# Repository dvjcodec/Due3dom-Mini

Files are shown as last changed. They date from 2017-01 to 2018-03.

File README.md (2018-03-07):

# DUE3DOM MINI

Modular 3D printer driver working as a shield for 32-bit ARM based Arduino DUE.

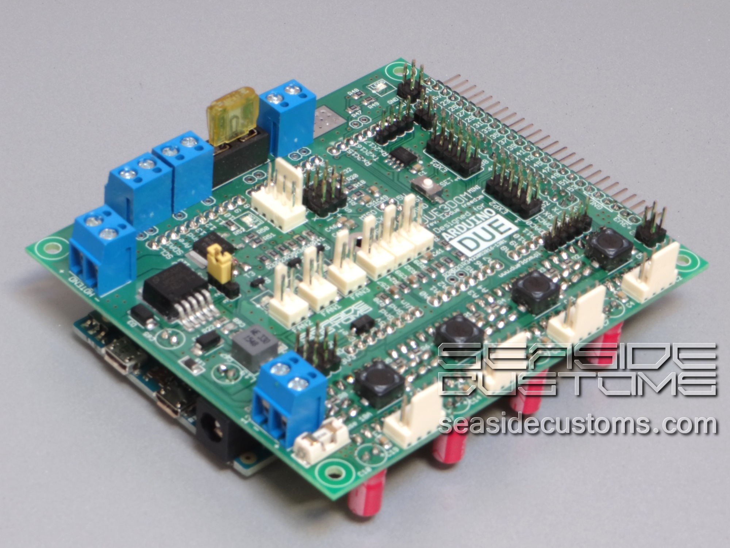
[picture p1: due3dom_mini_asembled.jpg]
Board


## Features:
* 20A channel for bed heating (20A fuse) with own power socket
* 10A channel for head heating (10A fuse) with own power socket
* up to 4 external A4988 compatible stepstick drivers (more on expansion port); jumper based step switching
* high current connectors for all power and driver sockets
* input for 4 thermistors (1x onboard; 3x external)
* PWM output for 3 fans
* 4-pin output for board cooling fan driven with signal based on onboard thermistor

## Connections

### Connecting LCD
* EXP1 on DUE3DOM to be connected with EXP2 on SmartController
* EXP2 on DUE3DOM to be connected with EXP1 on SmartController

### Stepstick drivers, motors and other peripherials
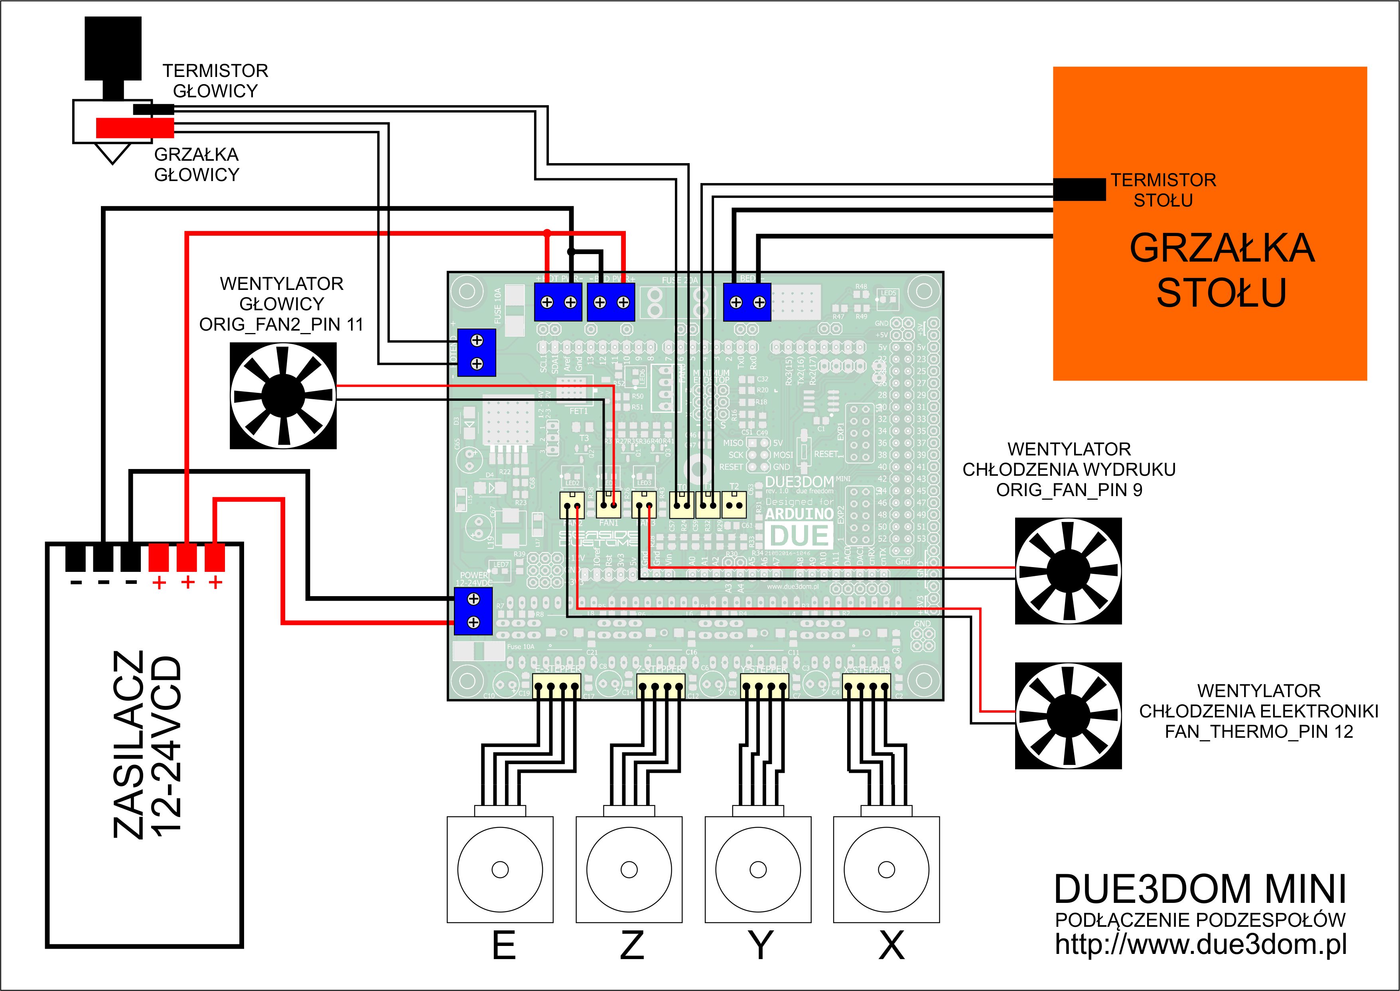
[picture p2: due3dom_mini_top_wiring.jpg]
Connections


## Issues

First board revision (A) needs two manual fixes:
* protection diode [#1](/../../issues/1)
* power on reset capacitor [#2](/../../issues/2)

## Firmware

Supported by official firmware:
* [Repetier](https://www.repetier.com/firmware/dev/index.php)
* [Marlin](https://github.com/esenapaj/Marlin)

## Support
* [Official Website [PL]](http://www.due3dom.pl/)
* [Forum thread [PL/EN]](http://www.fabrykator.pl/board/viewtopic.php?f=12&t=242)

## Where to buy?

* [Seaside Customs](http://fabrykator.pl/seasidecustoms/due3dom-elektronika-32bit-dla-drukarek-3d/)
* Contact: [@dvjcodec](https://github.com/dvjcodec/)

## Demo
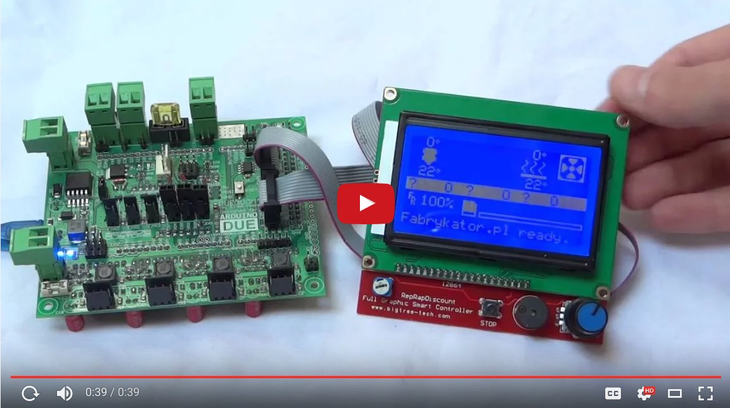
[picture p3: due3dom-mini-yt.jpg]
DUE3DOM MINI + LCD 128x64 - Marlin Firmware Demo (https://www.youtube.com/watch?v=12baxgj3plI "DUE3DOM MINI + LCD 128x64 - Marlin Firmware")


## License

[CC BY-NC 3.0](https://creativecommons.org/licenses/by-nc/3.0/)

## Authors

Krzysztof @ Seaside Customs

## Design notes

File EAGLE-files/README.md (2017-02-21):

Here you can find the EAGLE files for the board

Rev.2 changes (21.02.2017):
- add diode to DUE's power line
- add capacitor to RESET pin
- add 6-pin ISP onboard
- reduced few unused pins
- add 3-pin jumper for Stepstic's power logic (now can choose between 3V3 or 5V)
- driver's capacitors changed on SMD
- reduced onboard NTC100K thermistor
- reduced 4-pin slot for PWM fan
- few small changes (visual)
- microstep jumpers changed to solder-jumpers.

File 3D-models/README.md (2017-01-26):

Here you can find 3d models of the board itself

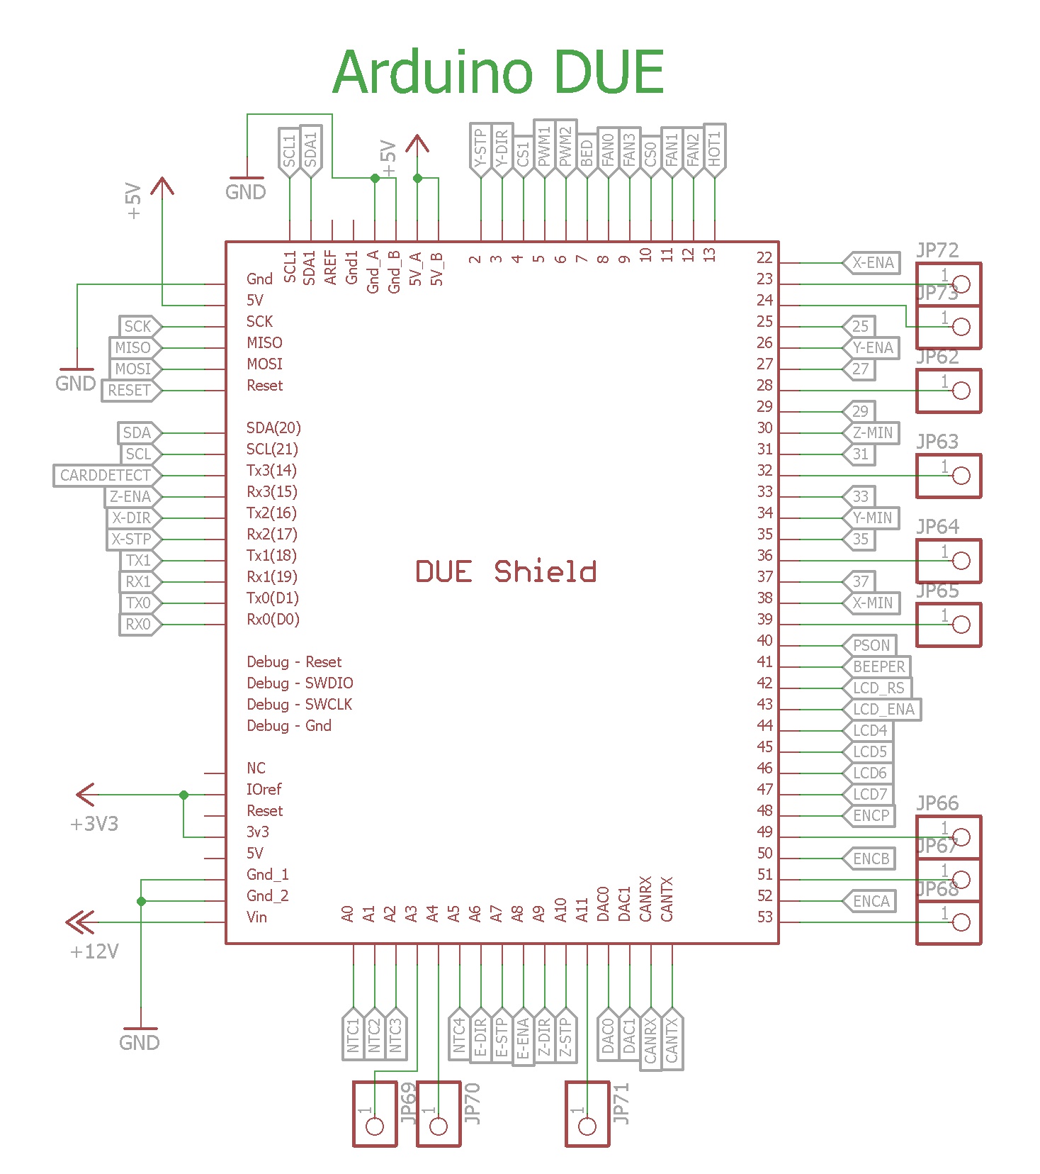
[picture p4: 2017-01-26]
due3dom-mini-pinout.jpg

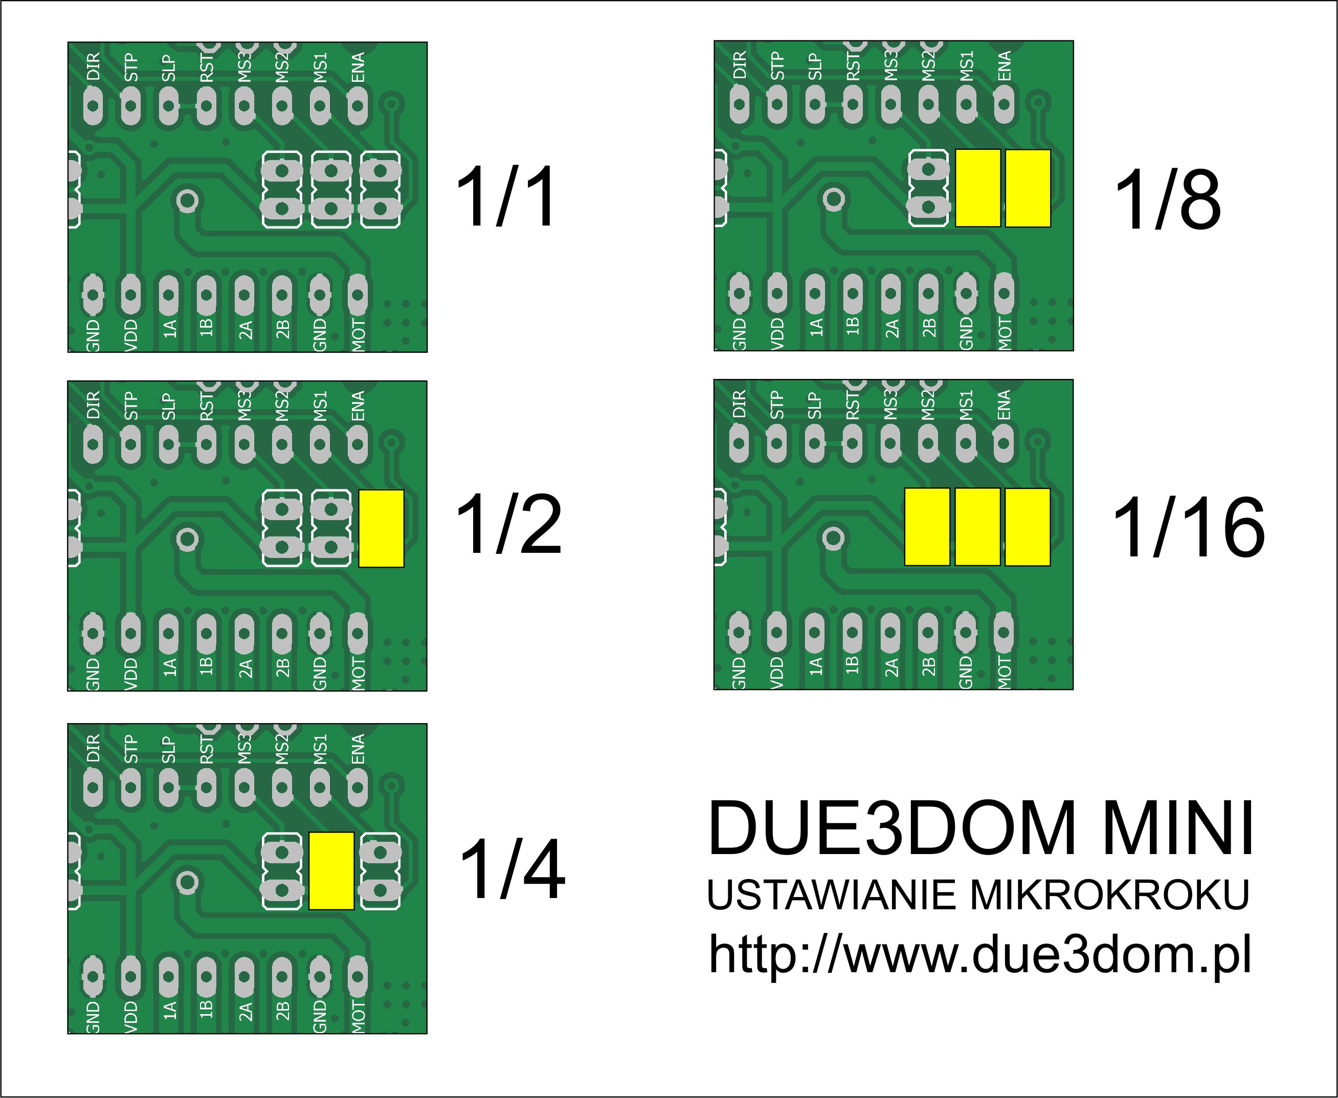
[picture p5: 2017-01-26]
due3dom_mini_microstep.jpg

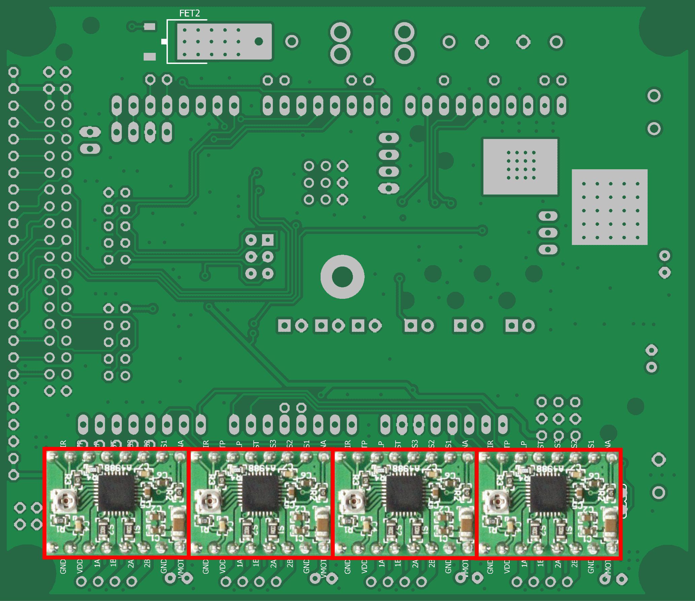
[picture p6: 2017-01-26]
due3dom_mini_bottom_stepstick.jpg

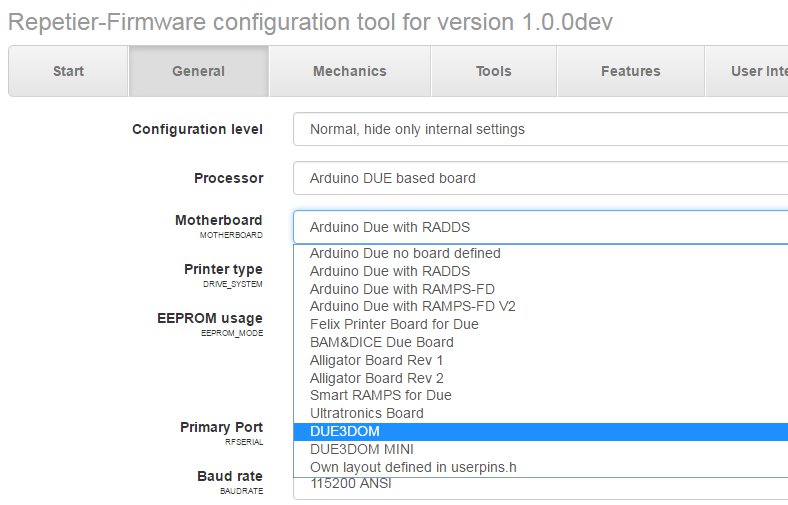
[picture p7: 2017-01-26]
due3dom_repetier.jpg

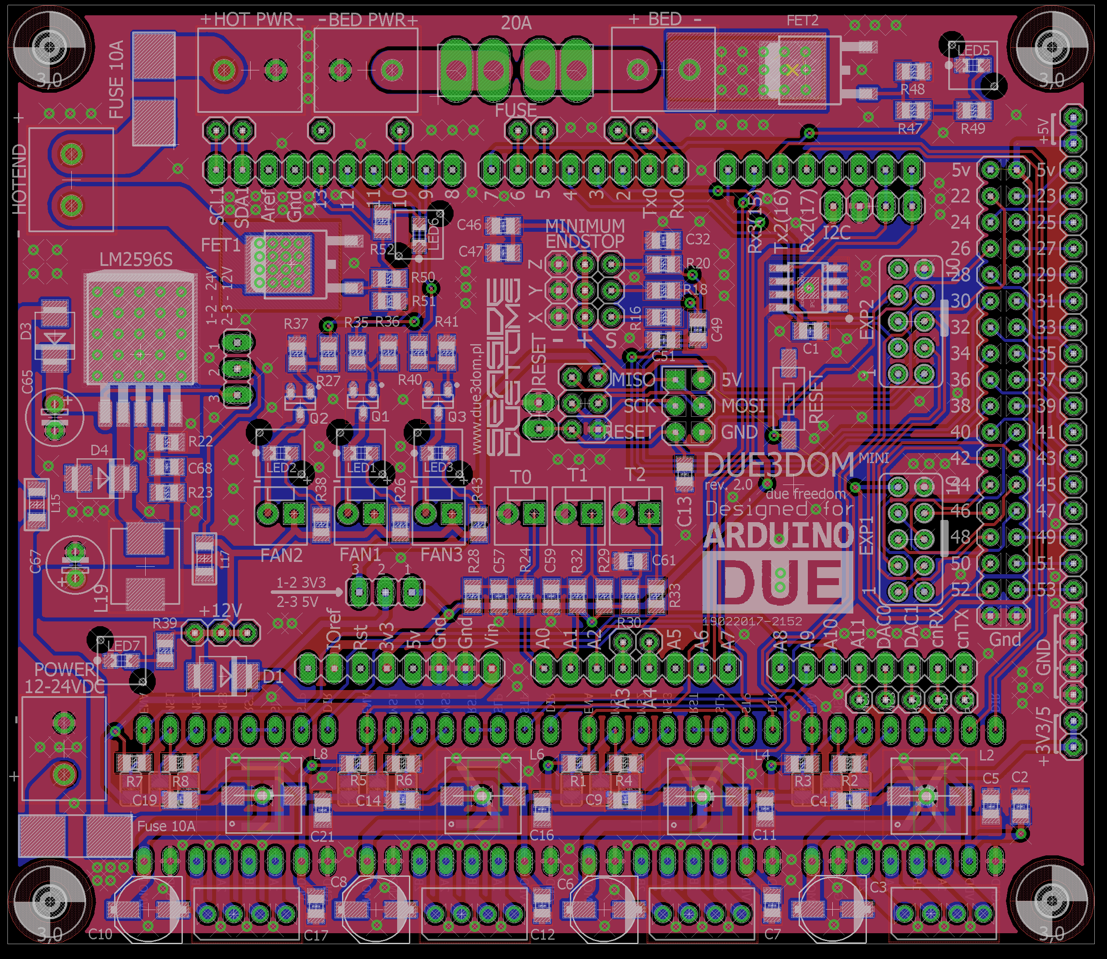
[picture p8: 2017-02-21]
EAGLE-files/Due3DOM_MINI_rev2_render_eagle.png

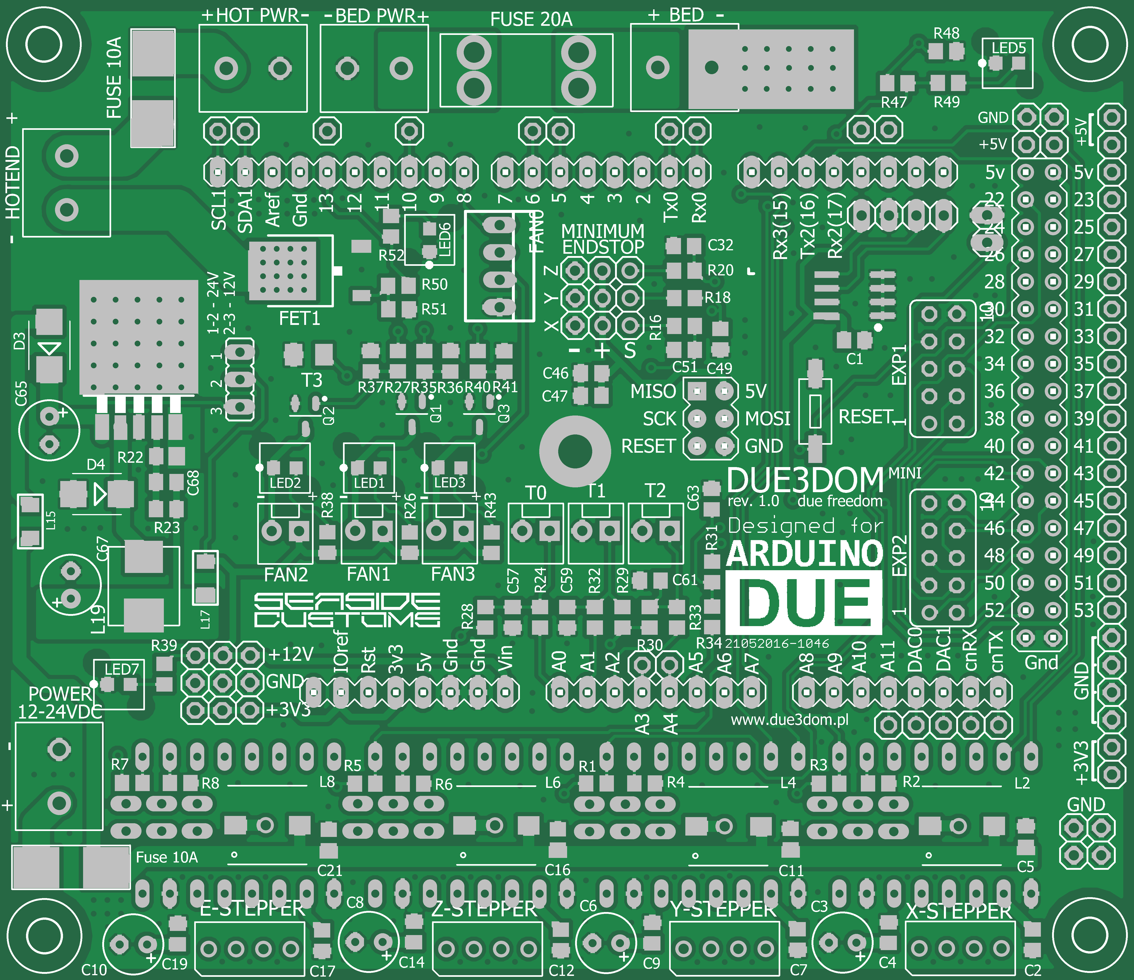
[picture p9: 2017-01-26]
EAGLE-files/eagleUp_DUE3DOM MINI 23052016-1301_board_top.png

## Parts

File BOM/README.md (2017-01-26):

Here you can find lists of components needed to assembly the board.

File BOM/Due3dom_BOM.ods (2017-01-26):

Nr części w układzie | STAN | Ilość | Wartość | Inne | Cena / szt. | Koszt 1 prototyp | Koszt na 5 prototypów | Ilość części na 5 prototypów | Link
AD1, AD2 | V | 2 | AD597 | SO8 | 24,37 | 48,74 | 243,7 | 10 | http://www.tme.eu/pl/details/ad597arz/przetworniki-temperatury/analog-devices/
C1, C2, C3, C4, C5, C6, C7, C8, C9, C11, C12, C13, C14, C15, C16, C17, C19, C21, C22, C24, C26, C27, C29, C31, C32, C35, C40, C43, C46, C48, C49, C50, C51 | V | 33 | 100nF 50V | C-EUC0805 | 0,0502 | 1,6566 | 8,283 | 165 | http://www.tme.eu/pl/details/08055c104jat2a/kondensatory-mlcc-smd-0805/avx/
C42, C45, C47 | V | 3 | 1uF | C-EUC0805 | 0,509 | 1,527 | 7,635 | 15 | http://www.tme.eu/pl/details/gcm21br71h105ka03l/kondensatory-mlcc-smd-0805/murata/
C57, C59, C61, C63 | V | 4 | 10uF | C-EUC0805 | 0,1 | 0,4 | 2 | 20 | http://allegro.pl/leon-kondensator-10uf-10u-0805-smd-20szt-i5640967204.html
C10, C3, C6, C8, C13, C15 | V | 6 | 100uF 35V elektrolit 6mm R2.5mm | Wurth 860010573007 | 0,175 | 1,05 | 5,25 | 30 | http://www.tme.eu/pl/details/sd1v107m6l011bb/kondensatory-elektrolityczne-tht-85c/samwha/
C65 | V | 1 | 100uF 35V elektrolit 6mm R3.5mm niskoimped. | RASTER 3.5 | 0,3104 | 0,3104 | 1,552 | 5 | http://www.tme.eu/pl/details/gf100_35/kondensatory-elektr-tht-niskoimpedan/samxon/
C67 | V | 1 | 220uF 25V elektrolit 6mm R2.5mm niskoimped. | RASTER 2.5 | 0,4695 | 0,4695 | 2,3475 | 5 | http://www.tme.eu/pl/details/gf220_25/kondensatory-elektr-tht-niskoimpedan/samxon/gf-220u25v/
C68 | V | 1 | 1nF | C-EUC0805 | 0,068 | 0,068 | 0,34 | 5 | http://www.tme.eu/pl/details/08051a102jat2a/kondensatory-mlcc-smd-0805/avx/
D3, D4 | V | 2 | B340B 3A 40V SMB | SCHOTTKY-DIODE SMD | 0,8833 | 1,7666 | 8,833 | 10 | http://www.tme.eu/pl/details/b340a-13-f/diody-schottky-smd/diodes-incorporated/
FET1, FET2, FET3 | V | 3 | IRLR8743 DPAK MOSFET | DPAK_N-CHANNEL_MOSFET TO252 | 2,78 | 8,34 | 41,7 | 15 | http://www.tme.eu/pl/details/irlr8743pbf/tranzystory-z-kanalem-n-smd/international-rectifier/
H1, H2, H3, H4, H5, H6 | V | 6 | GNIAZDO EXT 2.54MM 4PIN GOLDPIN | MOLEX 901200124 | 0,666 | 3,996 | 19,98 | 30 | http://www.tme.eu/pl/details/mx-90120-0124/listwy-i-gniazda-kolkowe/molex/901200124/
FAN1, FAN2, FAN3, NTC1, NTC2, NTC3, NTC4, TC-K1, TC-K2 | V | 9 | GNIAZDO 2PIN 2.54MM | 66100211622 + 661002151922 | 0,75 | 6,75 | 33,75 | 45
RST | V | 1 | GOLDPIN 2PIN | MOLEX 901200122 | 0,447 | 0,447 | 2,235 | 5 | http://www.tme.eu/pl/details/mx-90120-0122/listwy-i-gniazda-kolkowe/molex/901200122/
IC2 | V | 1 | 24LC256SN | 24LC256SN SO-08 | 2,89 | 2,89 | 14,45 | 5 | http://www.tme.eu/pl/details/24lc256-i_sng/pamieci-eeprom-szeregowe/microchip-technology/24lc256-isn/
J1, J2, J3, J4, J5, J6 | V | 6 | GNIAZDO SILNIKA 4PIN 2.54MM WURTH | 66100411622 + 661004151922 | 1,78 | 10,68 | 53,4 | 30
JP7, JP8, JP9, JP10, JP11, JP12, JP13 | V | 7 | GOLDPIN 3PIN 2.54MM | MOLEX 901200123 | 0,686 | 4,802 | 24,01 | 35 | http://www.tme.eu/pl/details/mx-90120-0123/listwy-i-gniazda-kolkowe/molex/901200123/
L1, L15, L17 | V | 3 | FERRITE BEAD 600R 2A | Wurth 74279218 | 0,27 | 0,81 | 4,05 | 15
L2, L4, L6, L8, L10, L12 | V | 6 | 8.2uH 2.7A WE-PD_7332/7345_PLASTIC_BASE | Wurth 74437349330 | 3,02 | 18,12 | 90,6 | 30
L19 | V | 1 | 33uH 1.9A 0.2R WE-LHMI_7030/7050 | Wurth 74437349330 | 2,8 | 2,8 | 14 | 5
LED3, LED4, LED6, LED7, LED8, LED9, LED10 | V | 7 | DIODA LED | LEDCHIPLED_0805 | 0,236 | 1,652 | 8,26 | 35 | http://www.tme.eu/pl/details/hsms-c170/diody-led-smd-kolorowe/avago/
P1, P2, P3, P4, P5, P7 | V | 6 | 691311700002 + 691352710002 | WURTH – terminale 5mm na zasilanie | 2,25 | 13,5 | 67,5 | 30 | http://katalog.we-online.de/en/em/TBL_5_00_3117_OPEN_VERTICAL_PCB_HEADER_69131170000X/691311700002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
Q1, Q2, Q3 | V | 3 | IRLML0030TRPBF SOT-23 |  | 0,4448 | 1,3344 | 6,672 | 15 | http://www.tme.eu/pl/details/irlml0030trpbf/tranzystory-z-kanalem-n-smd/international-rectifier/
R1, R2, R3, R4, R5, R6, R7, R8, R9, R10, R11, R12 | V | 12 | 100K | R-EU_R0805 | 0,02511 | 0,30132 | 1,5066 | 60 | http://www.tme.eu/pl/details/smd0805-100k/rezystory-smd-0805/royal-ohm/0805s8j0104t5e/
R14, R15, R16, R17, R18, R19, R20, R21, R36, R37, R41, R45, R48, R51 | V | 14 | 10K | R-EU_R0805 | 0,02511 | 0,35154 | 1,7577 | 70 | http://www.tme.eu/pl/details/smd0805-10k/rezystory-smd-0805/royal-ohm/0805s8j0103t5e/
R23 | V | 1 | 24K 1% | R-EU_R0805 | 0,0358 | 0,0358 | 0,179 | 5 | http://www.tme.eu/pl/details/smd0805-2k7-1%25/rezystory-smd-0805/royal-ohm/0805s8f2701t5e/
R24, R27, R32, R33, R34, R35, R40, R44, R47, R50 | V | 10 | 100R | R-EU_R0805 | 0,0478 | 0,478 | 2,39 | 50 | http://www.tme.eu/pl/details/crcw0805100rfkea/rezystory-smd-0805/vishay/
R26, R38, R39, R43, R22 | V | 5 | 2K7 1% | R-EU_R0805 | 0,0358 | 0,179 | 0,895 | 25 | http://www.tme.eu/pl/details/hp05-2k75%25/rezystory-smd-0805/royal-ohm/hp05w3j0272t5e/
R28, R29, R30, R31 | V | 4 | 4K7 | R-EU_R0805 | 0,05 | 0,2 | 1 | 20 | http://www.tme.eu/pl/details/hp05-4k75%25/rezystory-smd-0805/royal-ohm/hp05w3j0472t5e/
R46, R49, R52 | V | 3 | 470R | R-EU_R0805 | 0,05 | 0,15 | 0,75 | 15 | http://www.tme.eu/pl/details/hp05-470r5%25/rezystory-smd-0805/royal-ohm/hp05w3j0471t5e/
RESET | V | 1 | PRZYCISK RESET SMT | WIDE_TACT | 0,59 | 0,59 | 2,95 | 5 | http://www.tme.eu/pl/details/tactm-34n-f/mikroprzelaczniki-tact-pcb/ninigi/
S1, S2, S3, S4, S5, S7 | V | 6 | DIP SWITCH 3P 2.54MM SMT |  | 3,49 | 20,94 | 104,7 | 30 | http://www.tme.eu/pl/details/a6s-3101-h/przelaczniki-typu-dip-switch/omron/
STEPSTICK | V | 17 | GNIAZDO GOLDPIN 8PIN 2.54MM |  | 0,278 | 4,726 | 23,63 | 85 | http://www.tme.eu/pl/details/zl201-08g/listwy-i-gniazda-kolkowe/connfly/ds1021-1_8sf1-1/
EXP1, EXP2 | V | 2 | GOLDPIN 2X5PIN 2.54MM |  | 0,233 | 0,466 | 2,33 | 10 | http://www.tme.eu/pl/details/zl202-10g/listwy-i-gniazda-kolkowe/connfly/ds1021-2_5sf11/
U$11, U$12, U$13 | V | 3 | KEYSTONE_3568 | Keystone | 3,66 | 10,98 | 54,9 | 15 | http://www.tme.eu/pl/details/keys3568/bezpieczniki-gniazda-pcb/keystone/3568/
PCB | V | 1 | Merkar | Merkar | 61 | 61 | 305 | 5
Inne | V | 1 | Inne listwy i pierdoły i wysyłki | Inne | 30 | 30 | 150 | 5
IC5 LM2596S | V | 1 | LM2596S | LM2596S TO263-5 | 4,87 | 4,87 | 24,35 | 5 | http://allegro.pl/lispol-przetwornica-lm2596s-adj-3a-to263-i6169413325.html
Bezpiecznik | V | 3 | Bezpiecznik mini | Littlefuse | 3,84 | 11,52 | 57,6 | 15 | http://www.tme.eu/pl/details/0mini010.hxglo/bezpieczniki-samochodowe-mini/littelfuse/
 |  |  |  | RAZEM PLN NETTO |  | 278,90 | 1394,49
 |  |  |  | RAZEM PLN BRUTTO |  | 343,04 | 1715,22

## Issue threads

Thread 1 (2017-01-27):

Missing USB protection diode on PCB

arekm, 2017-01-27:
Current PCB is missing a diode that is supposed to prevent 5V from inverter to go back to USB.

Fix is to cut the trace and solder 12V/1A schottky diode.

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

Fix from http://www.fabrykator.pl/board/viewtopic.php?p=12128#p12128

dvjcodec, 2017-02-21:
Fixed in rev.2

Closed 2017-02-21.

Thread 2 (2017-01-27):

Delay arduino reset signal to reliably issue power on reset

arekm, 2017-01-27:
Missing capacitor is required to reliably boot arduino DUE microcontroller on power on event.

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

Fix from http://www.fabrykator.pl/board/viewtopic.php?p=12128#p12128

dvjcodec, 2017-02-21:
Fixed in rev.2

Closed 2017-02-21.

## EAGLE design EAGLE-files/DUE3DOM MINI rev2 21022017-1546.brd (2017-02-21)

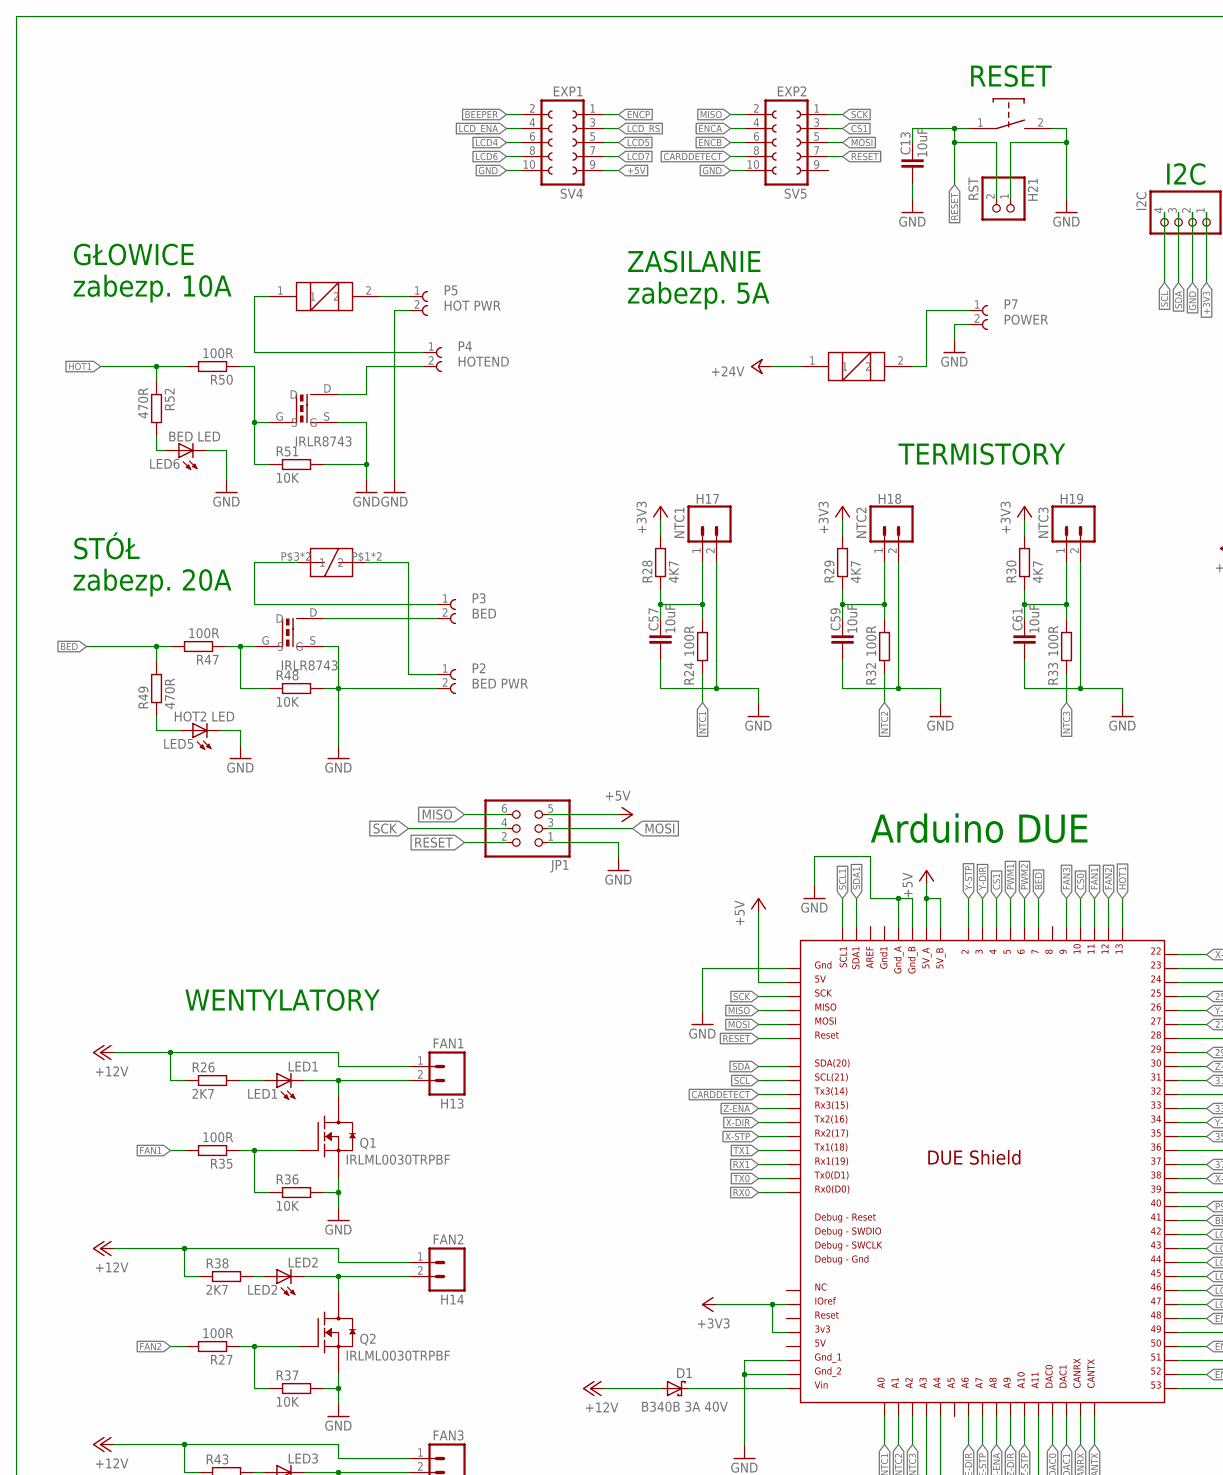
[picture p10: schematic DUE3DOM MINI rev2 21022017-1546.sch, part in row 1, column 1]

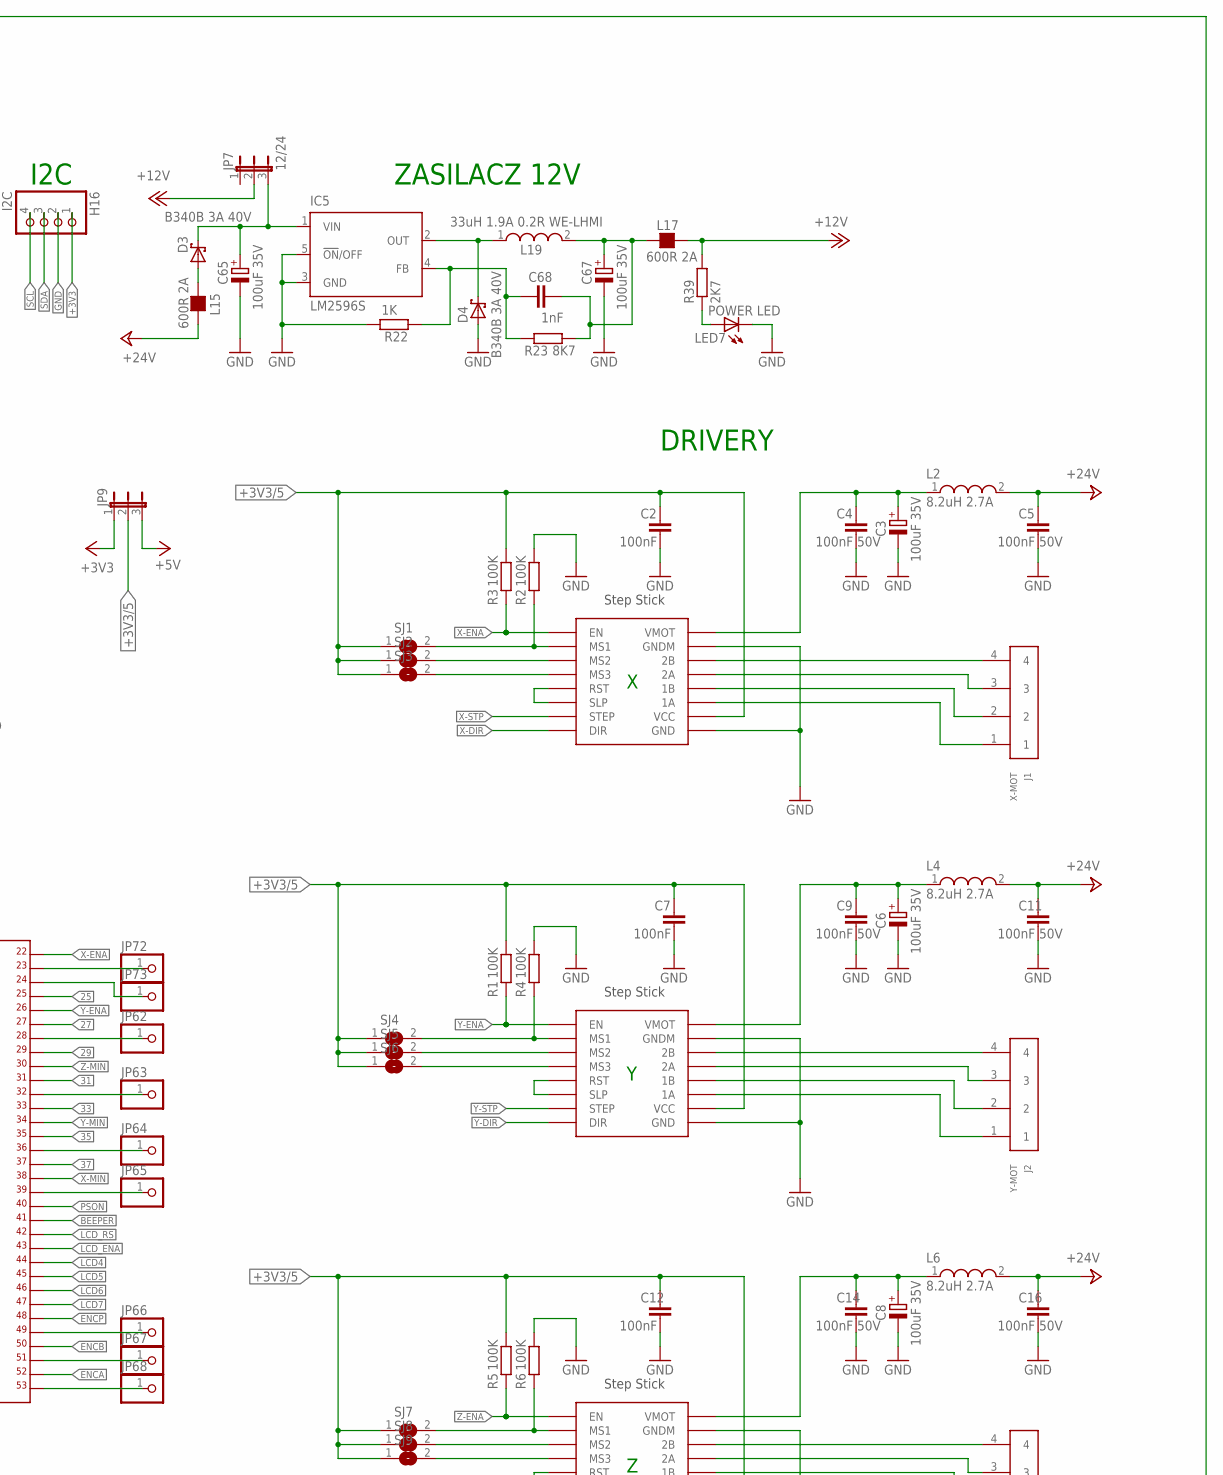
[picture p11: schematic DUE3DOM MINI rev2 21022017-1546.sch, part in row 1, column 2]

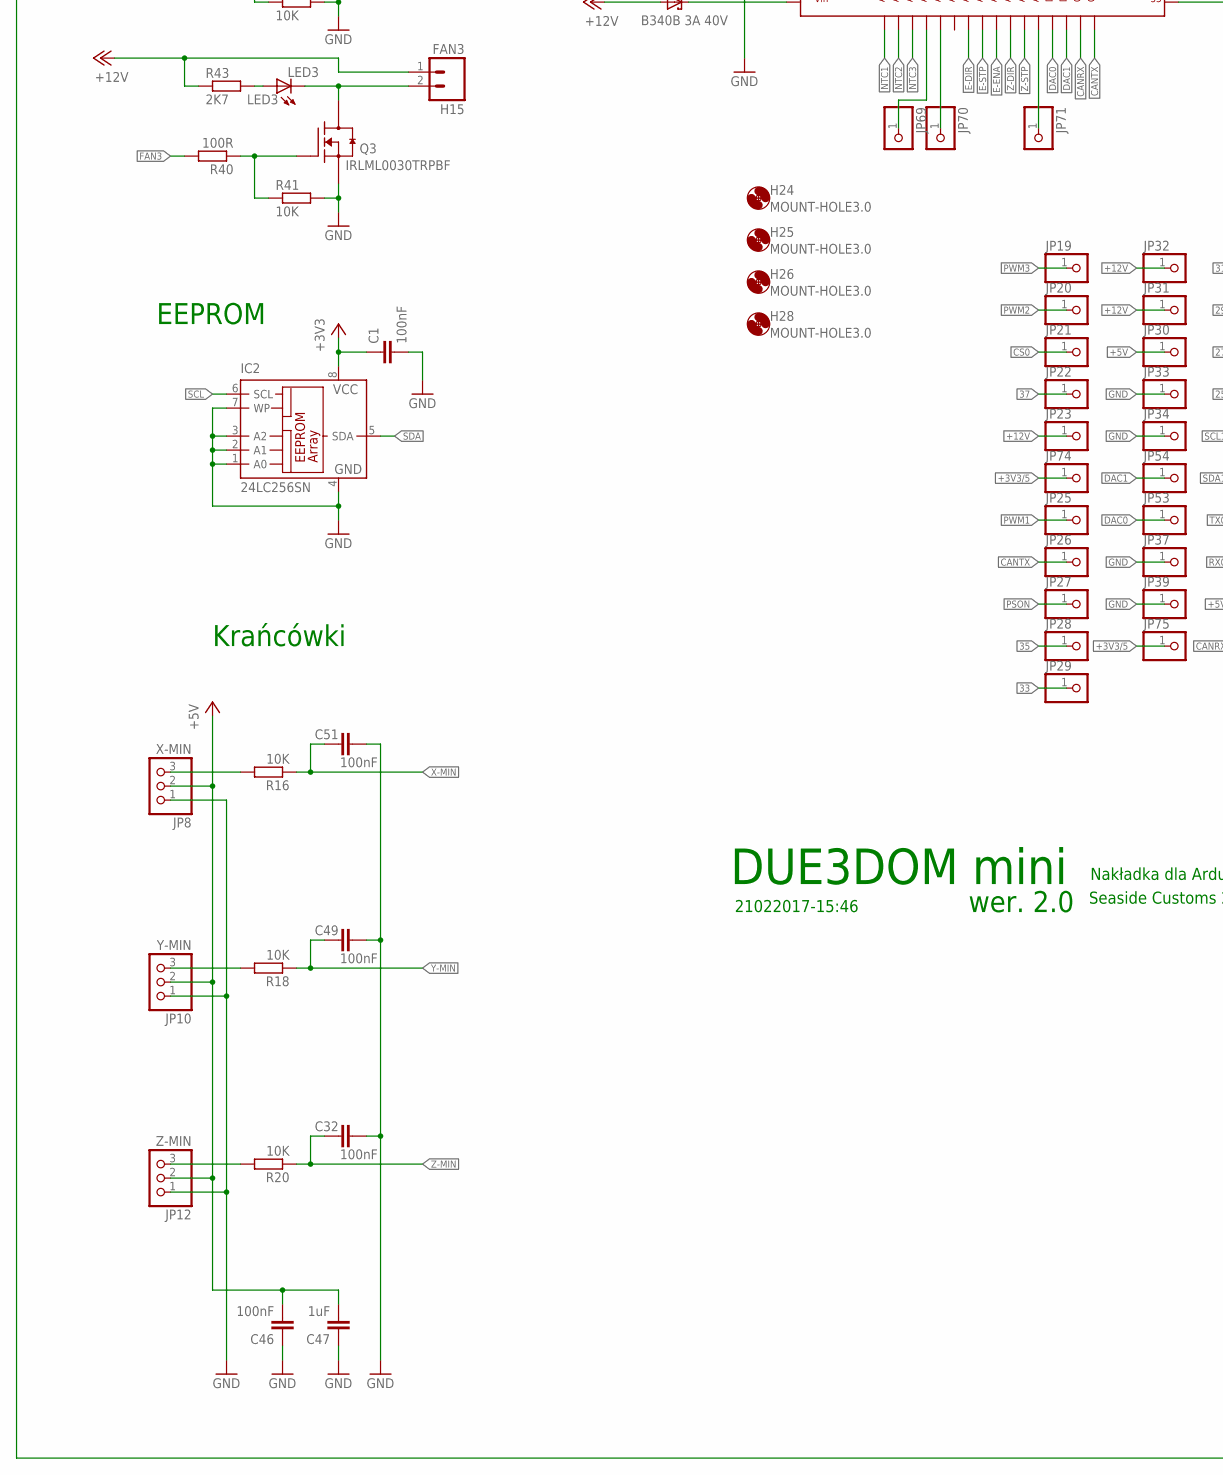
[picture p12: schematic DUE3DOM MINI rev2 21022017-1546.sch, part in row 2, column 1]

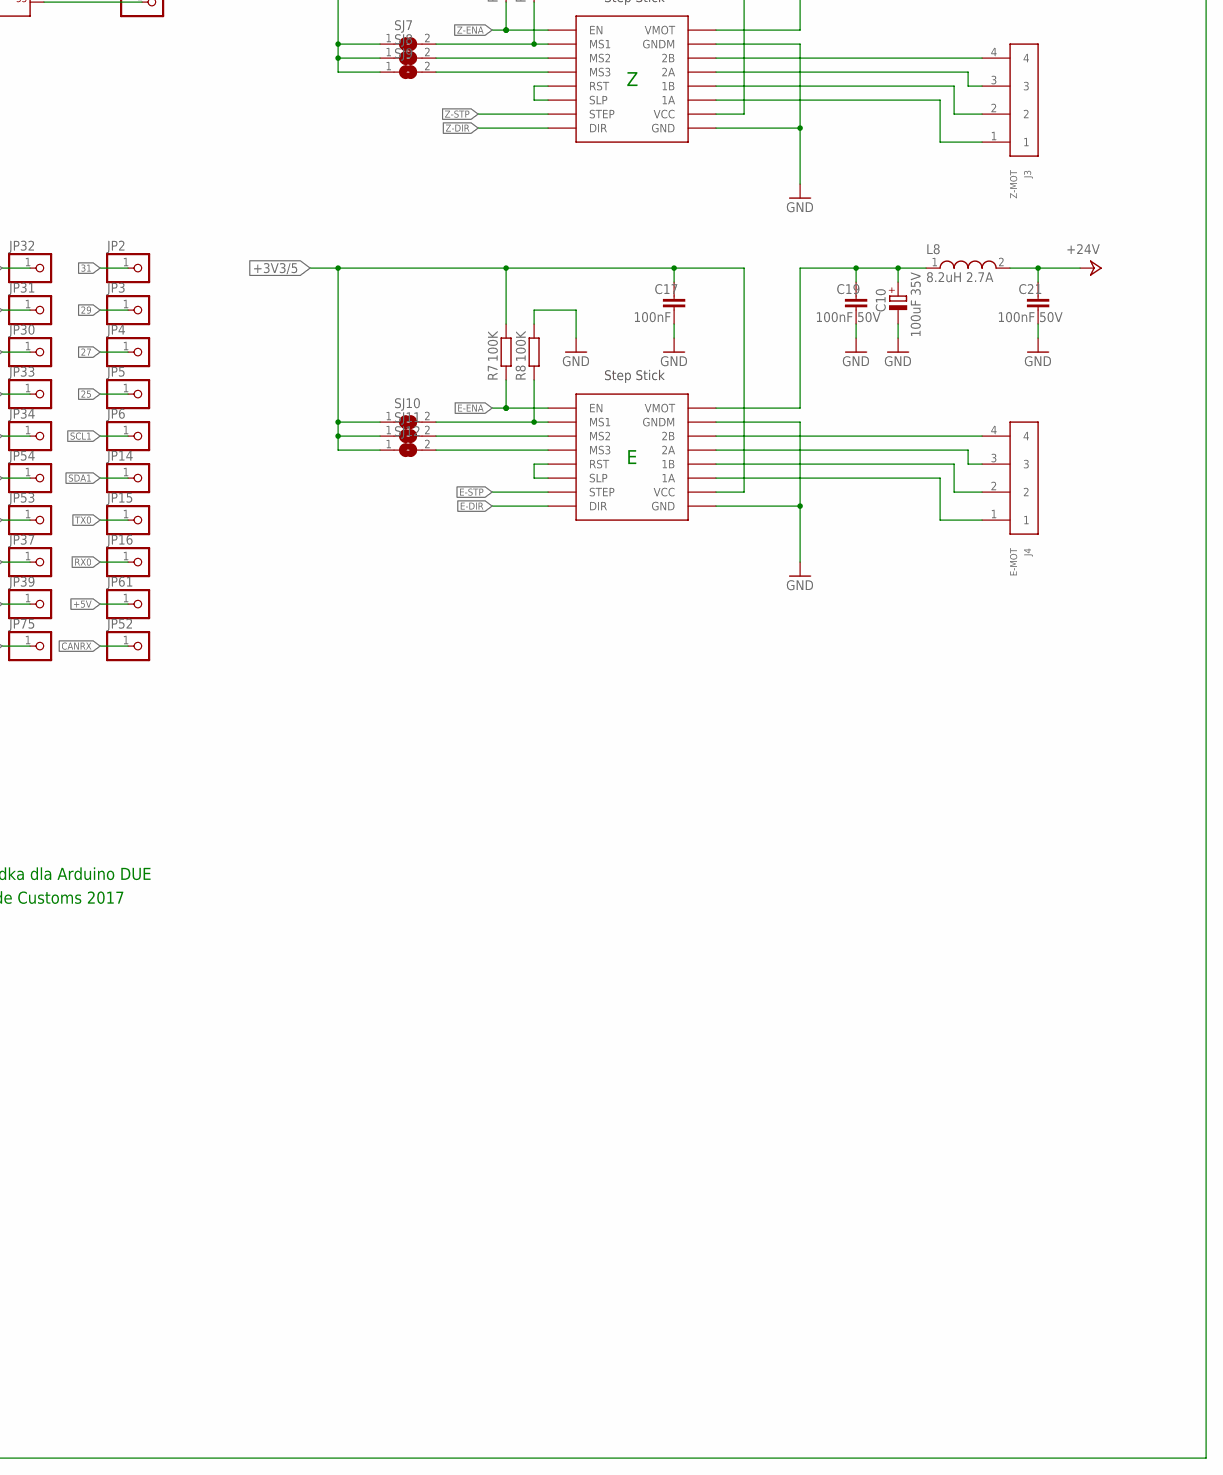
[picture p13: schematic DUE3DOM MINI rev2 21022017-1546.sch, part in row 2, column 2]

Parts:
C1, C2, C7, C12, C17, C32, C46, C49, C51: 100nF; C0805
C3, C6, C8, C10: 100uF 35V; PANASONIC_D
C4, C5, C9, C11, C14, C16, C19, C21: 100nF 50V; C0805
C13, C57, C59, C61: 10uF; C0805
C47: 1uF; C0805
C65, C67: 100uF 35V; E2,5-6
C68: 1nF; C0805
D1, D3, D4: B340B 3A 40V; SMB
FET1, FET2: DPAK_N-CHANNEL_MOSFET
FUSE: GNIAZDO_BEZPIECZNIKA_MINI_CHRL; FUSE_MINI_CHRL
H13: FAN1; MOLEX-1X2
H14: FAN2; MOLEX-1X2
H15: FAN3; MOLEX-1X2
H16: I2C; 1X04
H17: NTC1; MOLEX-1X2
H18: NTC2; MOLEX-1X2
H19: NTC3; MOLEX-1X2
H21: RST; 1X02
H24, H25, H26, H28: MOUNT-HOLE3.0; 3,0
IC2: 24LC256SN; SO-08
IC5: LM2596S; TO263-5
J1: X-MOT; 66100411622
J2: Y-MOT; 66100411622
J3: Z-MOT; 66100411622
J4: E-MOT; 66100411622
JP1: PINHD-2X3; 2X03
JP2, JP3, JP4, JP5, JP6, JP14, JP15, JP16, JP19, JP20, JP21, JP22, JP23, JP25, JP26, JP27, JP28, JP29, JP30, JP31, JP32, JP33, JP34, JP37, JP39, JP52, JP53, JP54, JP61, JP62, JP63, JP64, JP65, JP66, JP67, JP68, JP69, JP70, JP71, JP72, JP73, JP74, JP75: PINHD-1X1; 1X01
JP7: 12/24; JP2
JP8: X-MIN; 1X03
JP9: JP2E; JP2
JP10: Y-MIN; 1X03
JP12: Z-MIN; 1X03
L2, L4, L6, L8: 8.2uH 2.7A; WE-PD_7332/7345_PLASTIC_BASE
L15, L17: 600R 2A; L1206
L19: 33uH 1.9A 0.2R WE-LHMI; WE-LHMI_7030/7050
LED1: LED1; LED_0805_BIVAR_VLP-250-F
LED2: LED2; LED_0805_BIVAR_VLP-250-F
LED3: LED3; LED_0805_BIVAR_VLP-250-F
LED5: HOT2 LED; LED_0805_BIVAR_VLP-250-F
LED6: BED LED; LED_0805_BIVAR_VLP-250-F
LED7: POWER LED; LED_0805_BIVAR_VLP-250-F
P2: BED PWR; 691241710002
P3: BED; 691241710002
P4: HOTEND; 691241710002
P5: HOT PWR; 691241710002
P7: POWER; 691241710002
Q1, Q2, Q3: IRLML0030TRPBF; SOT95P280X135-3N
R1, R2, R3, R4, R5, R6, R7, R8: 100K; R0805
R16, R18, R20, R36, R37, R41, R48, R51: 10K; R0805
R22: 1K; R0805
R23: 8K7; R0805
R24, R27, R32, R33, R35, R40, R47, R50: 100R; R0805
R26, R38, R39, R43: 2K7; R0805
R28, R29, R30: 4K7; R0805
R49, R52: 470R; R0805
RESET: RESET; WIDE_TACT
SJ1, SJ2, SJ3, SJ4, SJ5, SJ6, SJ7, SJ8, SJ9, SJ10, SJ11, SJ12: SJ
STEPSTICK-X: STEP-STICK
STEPSTICK-Y: STEP-STICK
STEPSTICK-Z1, STEPSTICK-Z2: STEP-STICK
SV4: EXP1; FE05-2
SV5: EXP2; FE05-2
U$1: DUE(NORMAL)
U$2, U$3: FUSE_1808

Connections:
25: JP5.1, U$1.25
27: JP4.1, U$1.27
29: JP3.1, U$1.29
31: JP2.1, U$1.31
33: JP29.1, U$1.33
35: JP28.1, U$1.35
37: JP22.1, U$1.37
+3V3: C1.1, H16.1, IC2.8 (VCC), JP9.1, R28.2, R29.2, R30.2, U$1.3V3, U$1.IOREF
+3V3/5: C2.1, C7.1, C12.1, C17.1, JP9.2, JP74.1, JP75.1, R1.1, R3.1, R5.1, R7.1, SJ1.1, SJ2.1, SJ3.1, SJ4.1, SJ5.1, SJ6.1, SJ7.1, SJ8.1, SJ9.1, SJ10.1, SJ11.1, SJ12.1, STEPSTICK-X.VDD (VCC), STEPSTICK-Y.VDD (VCC), STEPSTICK-Z1.VDD (VCC), STEPSTICK-Z2.VDD (VCC)
+5V: C46.2, C47.2, JP1.5, JP8.2, JP9.3, JP10.2, JP12.2, JP30.1, JP61.1, SV4.9, U$1.5V_A, U$1.5V_B, U$1.GND_ICSP
+12V: D1.A, H13.1, H14.1, H15.1, JP7.2, JP23.1, JP31.1, JP32.1, L17.2, R26.1, R38.1, R39.2, R43.1
+24V: C5.1, C11.1, C16.1, C21.1, L2.2, L4.2, L6.2, L8.2, L15.1, U$3.1
BED: R47.2, R49.2, U$1.7
BEEPER: SV4.2, U$1.41
CANRX: JP52.1, U$1.CANRX
CANTX: JP26.1, U$1.CANTX
CARDDETECT: SV5.8, U$1.TX3
CS0: JP21.1, U$1.10
CS1: SV5.3, U$1.4
DAC0: JP53.1, U$1.DAC0
DAC1: JP54.1, U$1.DAC1
E-DIR: STEPSTICK-Z2.DIR, U$1.A6
E-ENA: R7.2, STEPSTICK-Z2.ENABLE (EN), U$1.A8
E-STP: STEPSTICK-Z2.STP (STEP), U$1.A7
ENCA: SV5.4, U$1.52
ENCB: SV5.6, U$1.50
ENCP: SV4.1, U$1.48
FAN1: R35.2, U$1.11
FAN2: R27.2, U$1.12
FAN3: R40.2, U$1.9
GND: C1.2, C2.2, C3.-, C4.2, C5.2, C6.-, C7.2, C8.-, C9.2, C10.-, C11.2, C12.2, C13.2, C14.2, C16.2, C17.2, C19.2, C21.2, C32.1, C46.1, C47.1, C49.1, C51.1, C57.2, C59.2, C61.2, C65.-, C67.-, D4.A, FET1.S, FET2.S, H16.2, H17.2, H18.2, H19.2, H21.1, IC2.1 (A0), IC2.2 (A1), IC2.3 (A2), IC2.4 (GND), IC2.7 (WP), IC5.3 (GND), IC5.5 (!ON!/OFF), JP1.1, JP8.1, JP10.1, JP12.1, JP33.1, JP34.1, JP37.1, JP39.1, LED5.C, LED6.C, LED7.C, P2.2, P5.2, P7.2, Q1.2 (S), Q2.2 (S), Q3.2 (S), R2.1, R4.1, R6.1, R8.1, R22.1, R36.2, R37.2, R41.2, R48.2, R51.2, RESET.2, STEPSTICK-X.GND (GNDM), STEPSTICK-X.GND1 (GND), STEPSTICK-Y.GND (GNDM), STEPSTICK-Y.GND1 (GND), STEPSTICK-Z1.GND (GNDM), STEPSTICK-Z1.GND1 (GND), STEPSTICK-Z2.GND (GNDM), STEPSTICK-Z2.GND1 (GND), SV4.10, SV5.10, U$1.5V_ICSP, U$1.GND_1, U$1.GND_2, U$1.GND_A, U$1.GND_B
HOT1: R50.2, R52.1, U$1.13
LCD4: SV4.6, U$1.44
LCD5: SV4.5, U$1.45
LCD6: SV4.8, U$1.46
LCD7: SV4.7, U$1.47
LCD_ENA: SV4.4, U$1.43
LCD_RS: SV4.3, U$1.42
MISO: JP1.6, SV5.2, U$1.MISO_ICSP
MOSI: JP1.3, SV5.5, U$1.MOSI_ICSP
unnamed: SJ5.2, STEPSTICK-Y.MS2
unnamed: C57.1, H17.1, R24.1, R28.1
unnamed: C61.1, H19.1, R30.1, R33.1
unnamed: P5.1, U$2.2
unnamed: STEPSTICK-X.RESET (RST), STEPSTICK-X.SLEEP (SLP)
unnamed: JP62.1, U$1.28
unnamed: JP63.1, U$1.32
unnamed: J1.4, STEPSTICK-X.2B
unnamed: FUSE.P$1 (1), FUSE.P$2 (1), P2.1
unnamed: R2.2, SJ1.2, STEPSTICK-X.MS1
unnamed: SJ2.2, STEPSTICK-X.MS2
unnamed: SJ3.2, STEPSTICK-X.MS3
unnamed: J1.3, STEPSTICK-X.2A
unnamed: J1.2, STEPSTICK-X.1B
unnamed: J1.1, STEPSTICK-X.1A
unnamed: C59.1, H18.1, R29.1, R32.1
unnamed: C3.+, C4.1, L2.1, STEPSTICK-X.VMOT
unnamed: JP64.1, U$1.36
unnamed: R4.2, SJ4.2, STEPSTICK-Y.MS1
unnamed: SJ6.2, STEPSTICK-Y.MS3
unnamed: SJ8.2, STEPSTICK-Z1.MS2
unnamed: STEPSTICK-Y.RESET (RST), STEPSTICK-Y.SLEEP (SLP)
unnamed: J2.4, STEPSTICK-Y.2B
unnamed: J2.3, STEPSTICK-Y.2A
unnamed: J2.2, STEPSTICK-Y.1B
unnamed: J2.1, STEPSTICK-Y.1A
unnamed: C6.+, C9.1, L4.1, STEPSTICK-Y.VMOT
unnamed: JP65.1, U$1.39
unnamed: JP8.3, R16.2
unnamed: R6.2, SJ7.2, STEPSTICK-Z1.MS1
unnamed: SJ9.2, STEPSTICK-Z1.MS3
unnamed: SJ11.2, STEPSTICK-Z2.MS2
unnamed: STEPSTICK-Z1.RESET (RST), STEPSTICK-Z1.SLEEP (SLP)
unnamed: J3.4, STEPSTICK-Z1.2B
unnamed: J3.3, STEPSTICK-Z1.2A
unnamed: J3.2, STEPSTICK-Z1.1B
unnamed: J3.1, STEPSTICK-Z1.1A
unnamed: C8.+, C14.1, L6.1, STEPSTICK-Z1.VMOT
unnamed: JP66.1, U$1.49
unnamed: JP10.3, R18.2
unnamed: R8.2, SJ10.2, STEPSTICK-Z2.MS1
unnamed: SJ12.2, STEPSTICK-Z2.MS3
unnamed: JP67.1, U$1.51
unnamed: STEPSTICK-Z2.RESET (RST), STEPSTICK-Z2.SLEEP (SLP)
unnamed: J4.4, STEPSTICK-Z2.2B
unnamed: J4.3, STEPSTICK-Z2.2A
unnamed: J4.2, STEPSTICK-Z2.1B
unnamed: J4.1, STEPSTICK-Z2.1A
unnamed: C10.+, C19.1, L8.1, STEPSTICK-Z2.VMOT
unnamed: JP68.1, U$1.53
unnamed: JP12.3, R20.2
unnamed: JP69.1, U$1.A3
unnamed: JP70.1, U$1.A4
unnamed: JP71.1, U$1.A11
unnamed: JP72.1, U$1.23
unnamed: JP73.1, U$1.24
unnamed: D1.C, U$1.VIN
unnamed: LED5.A, R49.1
unnamed: C68.1, IC5.4 (FB), R22.2, R23.1
unnamed: Q2.1 (G), R27.1, R37.1
unnamed: H14.2, LED2.C, Q2.3 (D)
unnamed: LED2.A, R38.2
unnamed: Q1.1 (G), R35.1, R36.1
unnamed: LED6.A, R52.2
unnamed: D3.A, L15.2
unnamed: H13.2, LED1.C, Q1.3 (D)
unnamed: LED1.A, R26.2
unnamed: Q3.1 (G), R40.1, R41.1
unnamed: H15.2, LED3.C, Q3.3 (D)
unnamed: LED3.A, R43.2
unnamed: FUSE.P$3 (2), FUSE.P$4 (2), P3.1
unnamed: FET2.G, R47.1, R48.1
unnamed: FET2.D, P3.2
unnamed: FET1.G, R50.1, R51.1
unnamed: FET1.D, P4.2
unnamed: P4.1, U$2.1
unnamed: LED7.A, R39.1
unnamed: P7.1, U$3.2
unnamed: C65.+, D3.C, IC5.1 (VIN), JP7.3
unnamed: D4.C, IC5.2 (OUT), L19.1
NTC1: R24.2, U$1.A0
NTC2: R32.2, U$1.A1
NTC3: R33.2, U$1.A2
PSON: JP27.1, U$1.40
PWM1: JP25.1, U$1.5
PWM2: JP20.1, U$1.6
PWM3: JP19.1
RESET: C13.1, H21.2, JP1.2, RESET.1, SV5.7, U$1.RESET_ICSP
RX0: JP16.1, U$1.RX0
RX1: U$1.RX1
SCK: JP1.4, SV5.1, U$1.SCK_ICSP
SCL: H16.4, IC2.6 (SCL), U$1.SCL
SCL1: JP6.1, U$1.SCL1
SDA: H16.3, IC2.5 (SDA), U$1.SDA
SDA1: JP14.1, U$1.SDA1
SUPP1: C67.+, C68.2, L17.1, L19.2, R23.2
TX0: JP15.1, U$1.TX0
TX1: U$1.TX1
X-DIR: STEPSTICK-X.DIR, U$1.TX2
X-ENA: R3.2, STEPSTICK-X.ENABLE (EN), U$1.22
X-MIN: C51.2, R16.1, U$1.38
X-STP: STEPSTICK-X.STP (STEP), U$1.RX2
Y-DIR: STEPSTICK-Y.DIR, U$1.3
Y-ENA: R1.2, STEPSTICK-Y.ENABLE (EN), U$1.26
Y-MIN: C49.2, R18.1, U$1.34
Y-STP: STEPSTICK-Y.STP (STEP), U$1.2
Z-DIR: STEPSTICK-Z1.DIR, U$1.A9
Z-ENA: R5.2, STEPSTICK-Z1.ENABLE (EN), U$1.RX3
Z-MIN: C32.2, R20.1, U$1.30
Z-STP: STEPSTICK-Z1.STP (STEP), U$1.A10

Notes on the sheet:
DRIVERY
Arduino DUE
EEPROM
Krańcówki
DUE3DOM mini
wer. 2.0
Nakładka dla Arduino DUE
Seaside Customs 2017
WENTYLATORY
GŁOWICE zabezp. 10A
STÓŁ zabezp. 20A
TERMISTORY
ZASILACZ 12V
I2C
RESET
ZASILANIE zabezp. 5A
21022017-15:46

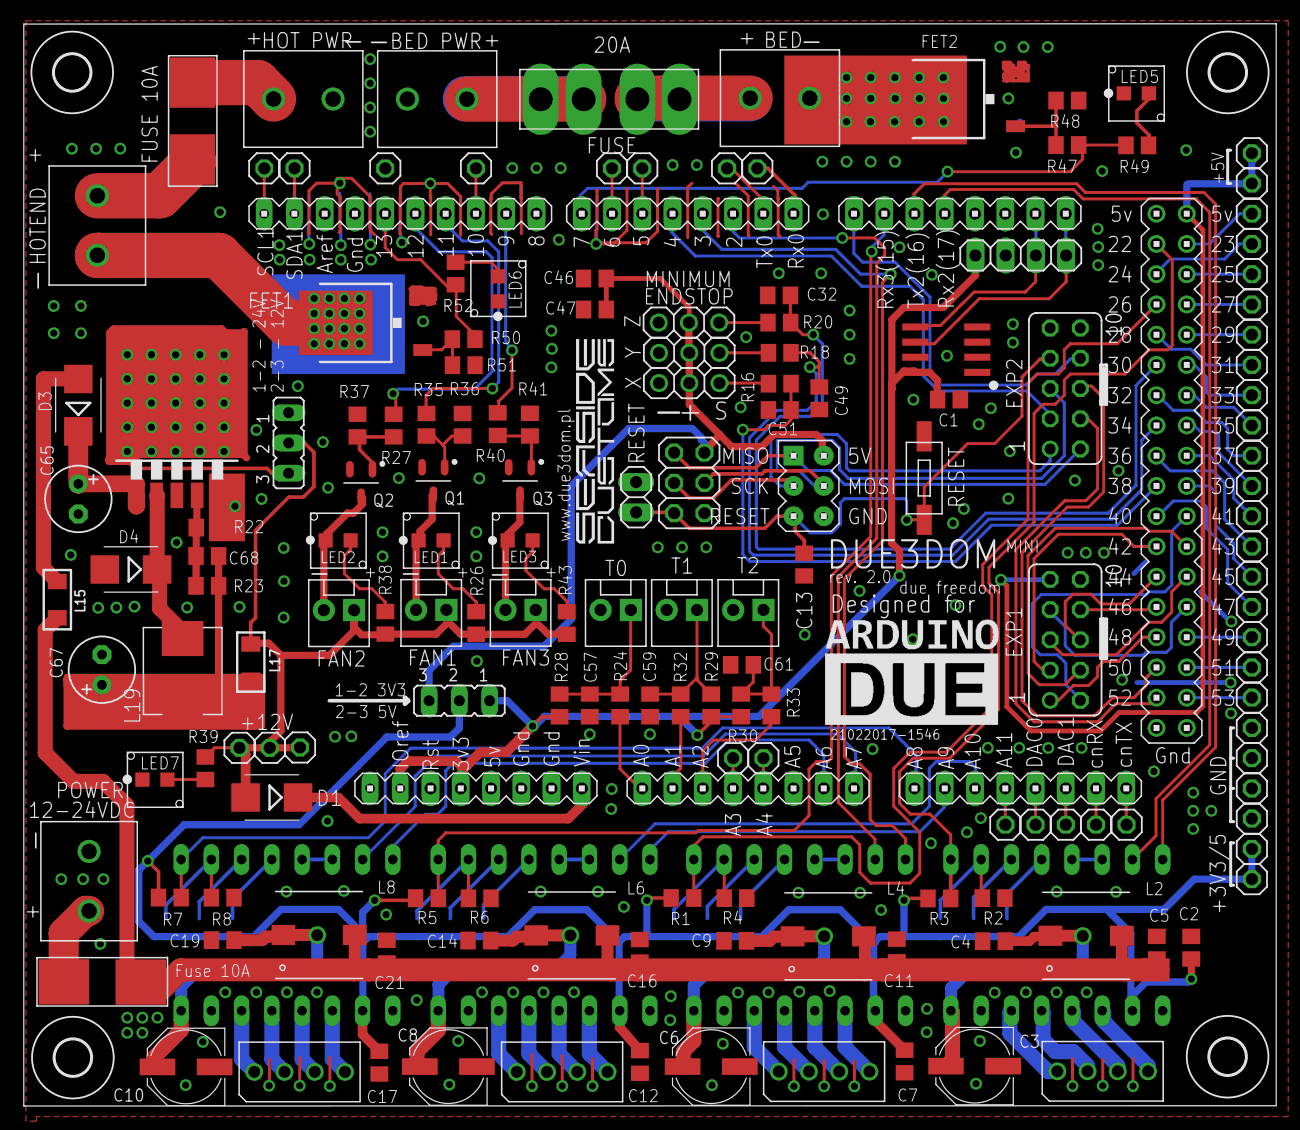
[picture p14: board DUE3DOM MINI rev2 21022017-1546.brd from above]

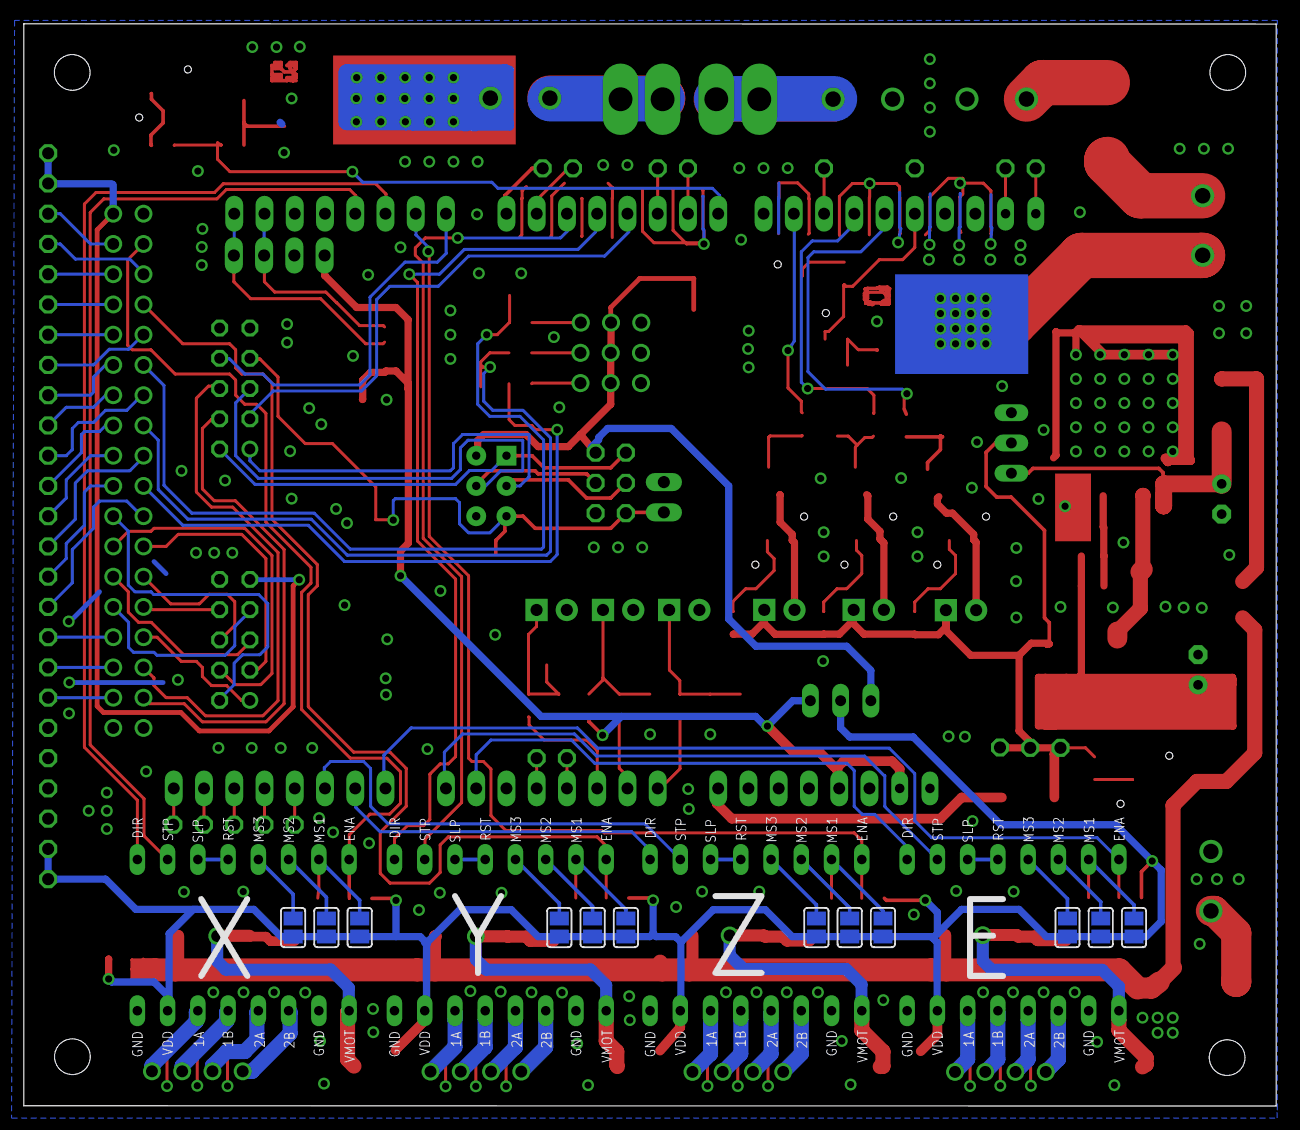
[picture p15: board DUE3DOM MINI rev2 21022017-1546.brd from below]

Board: 2 copper layers, 105.2 x 90.9 mm, 180 parts (16 on the bottom side), 147 nets.

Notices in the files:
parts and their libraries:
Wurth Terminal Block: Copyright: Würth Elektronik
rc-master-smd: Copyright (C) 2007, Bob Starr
